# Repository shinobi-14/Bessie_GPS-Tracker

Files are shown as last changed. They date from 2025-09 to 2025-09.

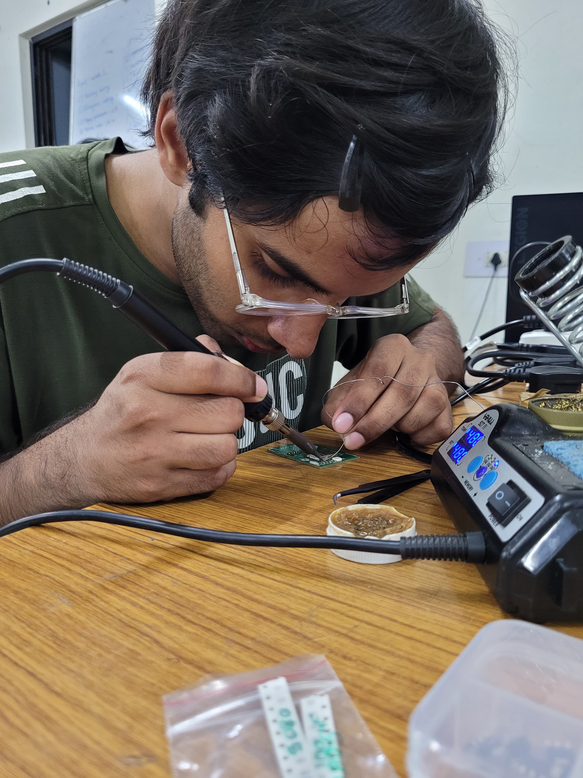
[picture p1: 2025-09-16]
media/images/Soldering Bessie.jpg

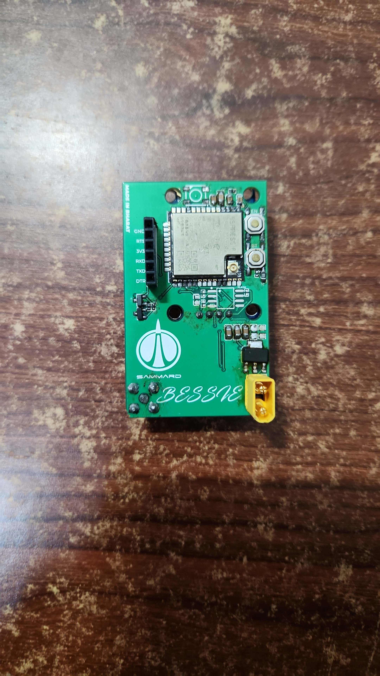
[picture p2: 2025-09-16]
media/images/BESSIE(2).jpeg

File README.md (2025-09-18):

# Bessie_GPS-Tracker
Bessie is the 1st gen custom-built tracker designed and developed in-house for the sounding rocket built for SACUP 24, Agneya.
<div align="center">
  
  
</div>

Bessie is powered by the ESP32-S3-N4R8 microcontroller, chosen for its familiar development environment and comprehensive functionality. It integrates a GPS module for high positional accuracy and a flash module to store data on board.

The telemetry consists of latitude, longitude, altitude, speed, heading, and satellite fix, which is transmitted over a 915 MHz frequency using a LoRa module to a ground station receiver, which is connected to a teammate's mobile phone.

This tracker aids in rocket recovery post-launch, serving as a redundant mechanism in the event of a main flight computer failure, still ensuring critical data availability.

# Repo Structure
The PCB was designed entirely in EasyEDA. I've included the design files, 3D files, gerber, schematic, test code and media files.

To replicate or explore this project, download the repository files and open them in EasyEDA, ensuring all file paths are correctly linked
    
	1. 3D_Files
	   .mtl & .obj exports -  can be used to visualize the PCB and its components in external 3D viewers or CAD tools.
	
	2. Design_Files
	   schematic & PCB .json - can be directly opened or imported in EasyEDA for editing and modification.
	
	3. Gerber_Files
		 PCB files for fabrication.
	
	4. media 
		 a. images 
            - contains PCB (bare and soldered), assembly & integration with the avionics bay pictures.
		 b. testing_vid
            - contains testing videos.
	
	5. BOM_Bessie.csv
	   List all components used in the project.
	
	6. Bessie_Schematics
	   Quick reference schematic.
	
	7. GPS Tracker code.ino 
	   ESP32 Firmaware code.
    
 # Components used
 - NEO-6M (Global Navigation Satellite System)
 - RFM95W (Lora module @ 915Mhz)
 - HJ-SMA507 (Right-angled THT SMA female connector)
 - W25Q128 (128-Mbit serial flash memory chip)
 - WS2812B (Addressable RGB Led)
 - AMS1117 (LDO Regulator @ 3.3V)
 - XT30 (Overload connector @ 30A)
 - FT232RL (UART module)
 - ESP32-S3-N4R8 (32bit microcontroller)

# Pinouts
#### _Communication Interface_
MOSI | MISO | SCK
:----: | :----: | :----:
IO23 | IO19 | 1018

#### _SPI Peripherals_
RFM95W | GPIO | W25Q128 | GPIO
:------: | :----: | :-------: | :----:
  MOSI | IO23 | MOSI    | IO23
  MISO | IO19 |   MISO  | IO19
   SCK | IO18 |   SCK   | IO18
   NSS |  IO5 |   CS    | IO25
 RESET | IO32 |   -     | -
   DI0 | IO33 |   -     | -

  #### _UART Peripherals: NEO-6M_
  TX | RX
:----: | :----: 
IO17 | IO16

# Reference Materials
- [ESP32 Documentation](https://www.espressif.com/sites/default/files/documentation/esp32-s3-wroom-1_wroom-1u_datasheet_en.pdf)
- [Product Specification for Resistors](https://www.scribd.com/document/399006761/RT0603BRD0710KL) (This helps in selecting the appropriate package size for different applications)
- [Pull-up resistors tutorial](https://learn.sparkfun.com/tutorials/pull-up-resistors/all#:~:text=In%20other%20words%2C%20a%20small,pin%20reads%20close%20to%20VCC)
- [EEVblog Youtube](youtube.com/watch?time_continue=1&v=BcJ6UdDx1vg&embeds_referring_euri=https%3A%2F%2Fwww.eevblog.com%2F&source_ve_path=Mjg2NjY) (Highly recommended)
- [EasyEDA Guide](https://docs.easyeda.com/en/)
- [DroneBot Workshop Youtube](https://www.youtube.com/watch?v=YQ7aLHCTeeE&t=90s) (Highly Recommended)
- [geeksforgeeks](https://www.geeksforgeeks.org/operating-systems/what-is-flash-memory/)
- [Phil's Lab Youtube](https://www.youtube.com/watch?v=WPT96w3eLAM) (Highly Recommended)

Author: Prithvi Raj Singh (shinobi-14)

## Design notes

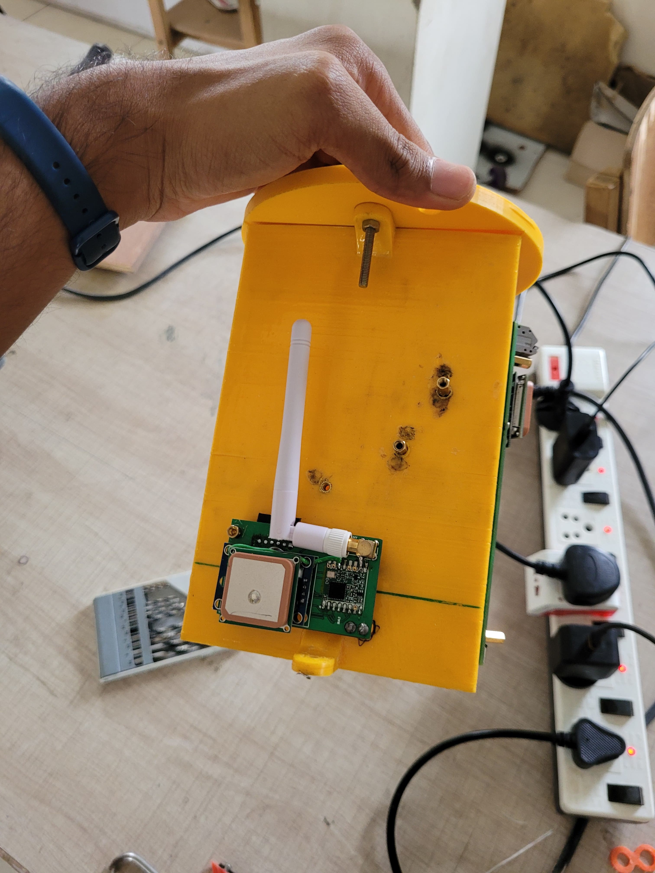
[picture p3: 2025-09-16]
media/images/BESSIE integrated on Avionics Bay.jpg

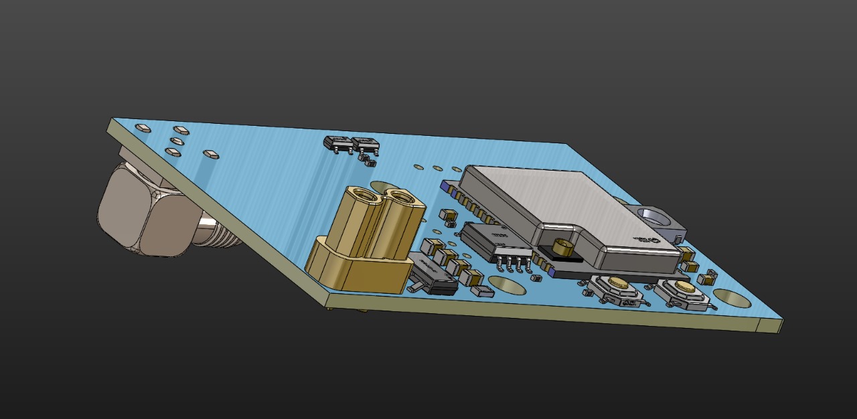
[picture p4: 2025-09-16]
media/images/3D_BESSIE.jpg

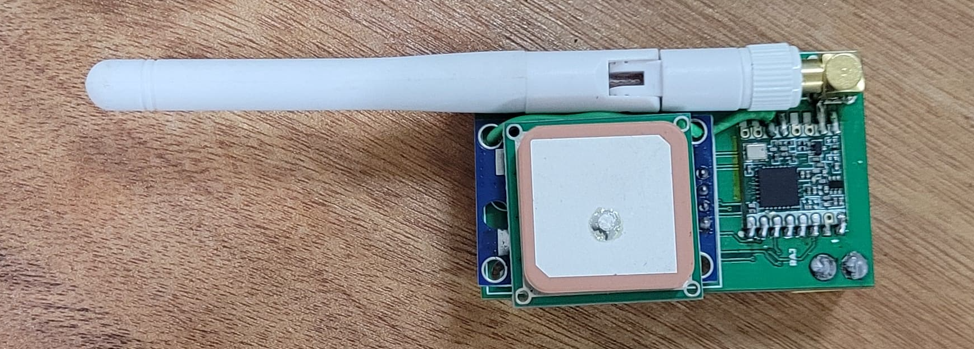
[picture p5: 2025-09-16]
media/images/BESSIE(1).png

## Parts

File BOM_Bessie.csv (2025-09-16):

ID | Name | Designator | Quantity | Manufacturer Part
1 | HJ-SMA507 | ANT | 1 | HJ-SMA507
2 | TS-1187A-B-A-B | BOOT_BT,EN_BT | 2 | TS-1187A-B-A-B
3 | 10u | C1 | 1
4 | 0.1u | C2,C3 | 2
5 | 10uF | C4,C5,C6,C7 | 4 | GRM21BR61H106KE43L
6 | 100nF | C8 | 1
7 | 0.1uF | C9 | 1 | GRM21BR61H106KE43L
8 | T2 | EN_TN1 | 1 | BC847
9 | 10kΩ | EN_TRANS_RES1,IO1_TRANS_RES | 2 | SCR0402F10K
10 | ESP32-WROOM-32U | ESP1 | 1 | ESP32-WROOM-32U-N4
11 | W25Q128JVSIQ | FLASH | 1 | W25Q128JVSIQ
12 | T1 | IO1_TN1 | 1 | BC847
13 | WS2812B-B/W | LED1 | 1 | WS2812B-B/T
14 | DL-RFM95 | LORA | 1 | DL-RFM95-868M
15 | GY-GPS6MV2_ADJUSTED | NEO-6M | 1
16 | Female Header | P2 | 1 | 2.54-1*6P母
17 | 1k | R1,R2,R4,R5,R6 | 5
18 | 0 | R3 | 1
19 | XT30 | U1 | 1 | XT30U-F
20 | AMS1117-3.3V | U2 | 1 | AMS1117-3.3V

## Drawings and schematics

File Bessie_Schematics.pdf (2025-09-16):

IO0 25 IO4 26 IO16 27 IO17 28 IO5 29 IO18 30 IO19 31 NC 32 IO21 33 RXD0 34 TXD0 35 IO22 36 IO23 37 GND 38

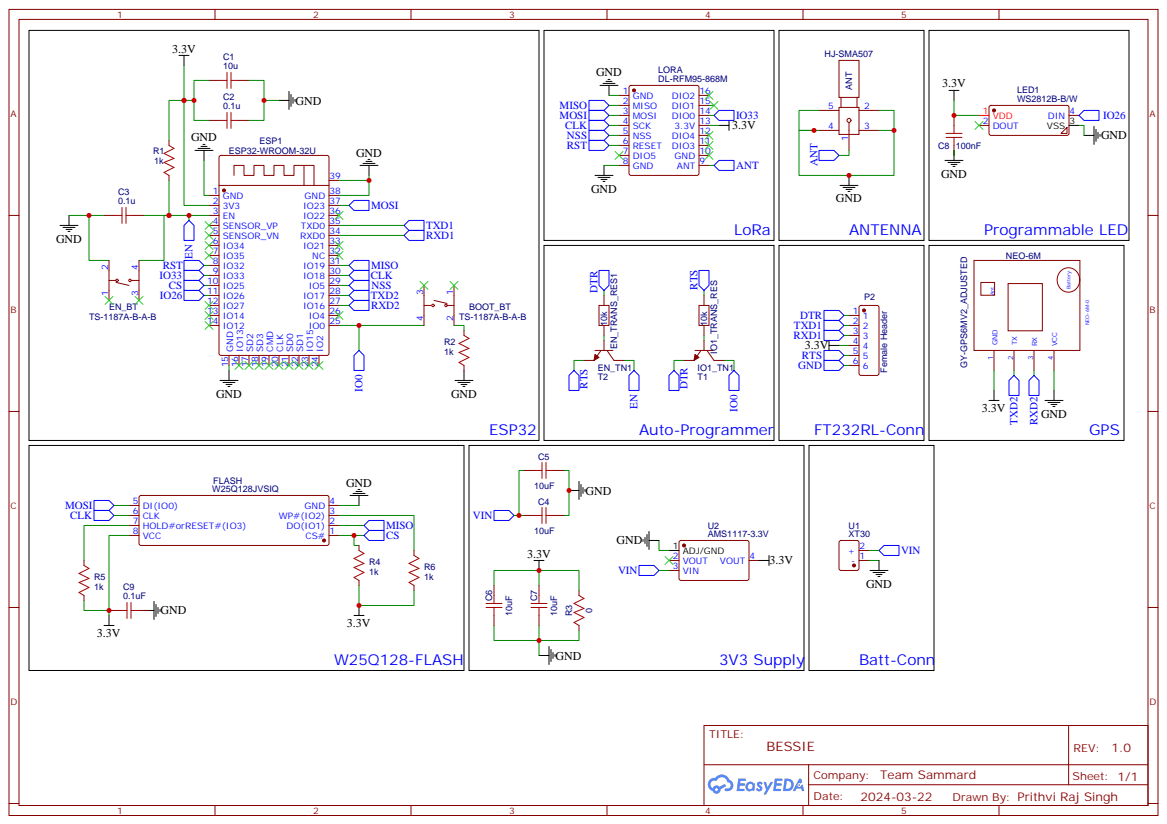
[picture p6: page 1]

Drawn By: Prithvi Raj Singh

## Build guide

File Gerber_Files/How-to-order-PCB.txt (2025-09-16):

How to Order PCB

Please refer to:
https://docs.easyeda.com/en/PCB/Order-PCB

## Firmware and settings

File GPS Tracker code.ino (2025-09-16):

#include <LoRa.h>
#include <TinyGPS++.h>
#include "FastLED.h"

#define NUM_LEDS 1
#define DATA_PIN 26

TinyGPSPlus tinyGPS;
#define GPS_BAUD 9600

// Use HardwareSerial on ESP32 (UART2)
HardwareSerial GPSSerial(2);

CRGB leds[NUM_LEDS];

void setup() 
{
  Serial.begin(115200);
  GPSSerial.begin(GPS_BAUD, SERIAL_8N1, 17, 16); // RX=17 (GPS TX), TX=16 (GPS RX)

  // LED setup
  FastLED.addLeds<WS2812B, DATA_PIN, GRB>(leds, NUM_LEDS);
  FastLED.setBrightness(64);

  // LoRa setup
  Serial.println("LoRa Sender");
  LoRa.setPins(5, 32, 33);
  LoRa.setTxPower(20);
    
  if (!LoRa.begin(915E6)) {   // unchanged
    Serial.println("Starting LoRa failed!");
    while (1);
  }
  LoRa.setSignalBandwidth(125000); 
}  

void ledburn()
{
  leds[0] = CRGB(24,0,0);
  FastLED.show();
  delay(500);
  leds[0] = CRGB(0,24,0);
  FastLED.show();
  delay(500);
  leds[0] = CRGB(0,0,24);
  FastLED.show();
  delay(500);
  leds[0] = CRGB(12,0,12);
  FastLED.show();
  delay(500);
  leds[0] = CRGB(12,12,0);
  FastLED.show();
  delay(500);
  leds[0] = CRGB(0,12,12);
  FastLED.show();
  delay(500);
  leds[0] = CRGB(8,8,8);
  FastLED.show();
  delay(500);
}

void loraprint()
{
  LoRa.beginPacket();
  LoRa.println("This is Bessie");
  LoRa.print("Lat: "); LoRa.println(tinyGPS.location.lat(), 6);
  LoRa.print("Long: "); LoRa.println(tinyGPS.location.lng(), 6);
  LoRa.print("Alt: "); LoRa.println(tinyGPS.altitude.feet());
  LoRa.print("Course: "); LoRa.println(tinyGPS.course.deg());
  LoRa.print("Speed: "); LoRa.println(tinyGPS.speed.kmph());
  LoRa.print("Sats: "); LoRa.println(tinyGPS.satellites.value());
  LoRa.print("Date: ");
  LoRa.print(tinyGPS.date.day());
  LoRa.print("/");
  LoRa.print(tinyGPS.date.month());
  LoRa.print("/");
  LoRa.println(tinyGPS.date.year());
  LoRa.endPacket();
}

void loop() 
{
  ledburn();
  loraprint();
  smartDelay(100);
}
  
static void smartDelay(unsigned long ms)
{
  unsigned long start = millis();
  do
  {
    while (GPSSerial.available())
      tinyGPS.encode(GPSSerial.read());
  }
  while (millis() - start < ms);
}

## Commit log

2025-09-16 adding PCB files
2025-09-16 adding schematics
2025-09-16 adding PCB fab files
    [Drill_NPTH_Through.DRL, Drill_PTH_Through.DRL, Drill_PTH_Through_Via.DRL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]
2025-09-16 attaching media folder
2025-09-16 adding BOM
    [BOM_Bessie.csv]
